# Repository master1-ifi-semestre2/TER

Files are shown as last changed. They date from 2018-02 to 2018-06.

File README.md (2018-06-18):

# Robot avec détection d’obstacles

Ce tutoriel vous guidera pas à pas dans la réalisation d'un robot explorateur détecteur d'obstacles.
Nous allons en réalité utiliser deux robots : 1 robot principal et 1 robot secondaire qui aura pour objectif de suivre le robot leader.

### Composants et outils
##### Robot de tête
Pour pouvoir construire le leader, vous aurez besoin de :
- 1 Arduino UNO (ou un autre type de microcontrôleur)
- 1 Shield Motor (Adafruit ou un autre type)
- 2 Moteurs avec roues adaptées aux moteurs
- 1 roue pivot
- 6 ultrasonic sensor HC-RC04
- 1 module emetteur sans fils 433Mhz (pour la communication radio fréquence)
- 1 boîtier pour 5 piles AA (de 1,2 V)
- des cables jumper
- 1 mini breadboard
- 1 chassis

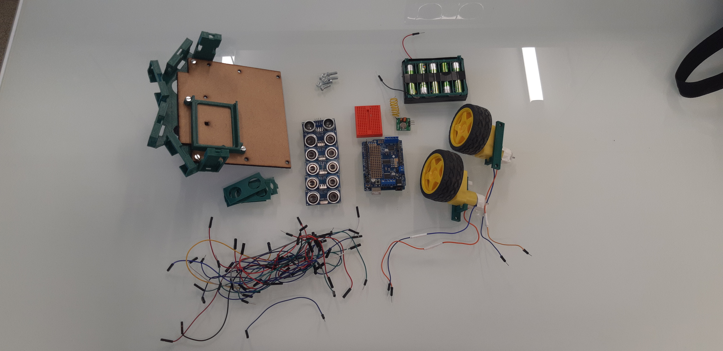
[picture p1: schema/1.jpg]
Les differents composant


##### Robot de queue
Pour construire le robot follower, vous aurez besoin de:
- 1 Arduino UNO
- 1 Shield Motor
- 2 Moteurs & leurs roues
- 1 roue libre
- 1 détecteurs de distance (ultrasonic sensor HC-RC04)
- 1 module récepteur sans fils 433Mhz (pour la communication radio fréquence)
- 1 boîtier pour 5 piles AA (de 1,2 V)
- des cables jumper
- 1 mini breadboard
- 1 chassi

#### Outils
- Une découpeuse Laser (utilisé pour faire le chassis des deux robots)
- Une imprimante 3D (utilisé pour imprimer certain accessoirs comme le pare-choc et le boîtier à piles...).
- Un éventuel kit de soudure si vos fils en ont besoin.

## Assembler le robot
Après vous être procuré tout ce materiel, commencez par retourner le chassis, puis fixez les moteurs.
<p align="center">
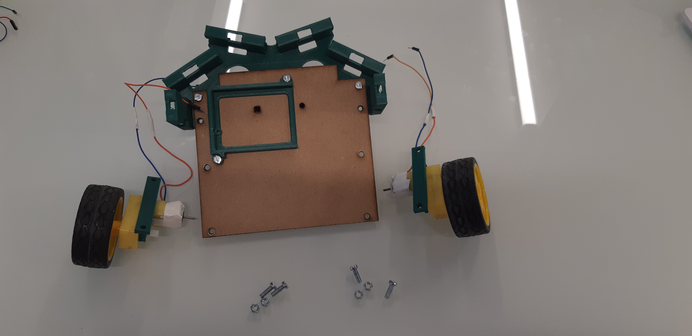
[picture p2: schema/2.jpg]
Chassi avec les Moteurs

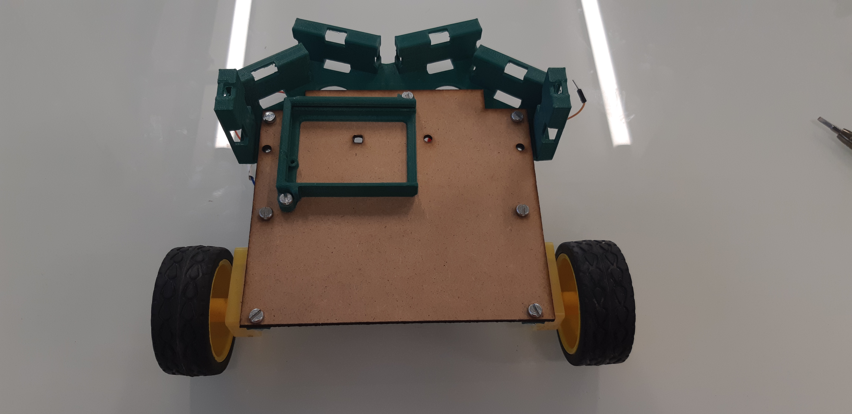
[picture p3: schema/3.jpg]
Moteurs monté

</p>

Montez ensuite le nez, puis les capteurs à ultrason. Nous conseillons de renverser un des capteurs centraux (pins vers le haut et pins vers le bas)afin d'éviter les interférence entre eux.

<p align="center">
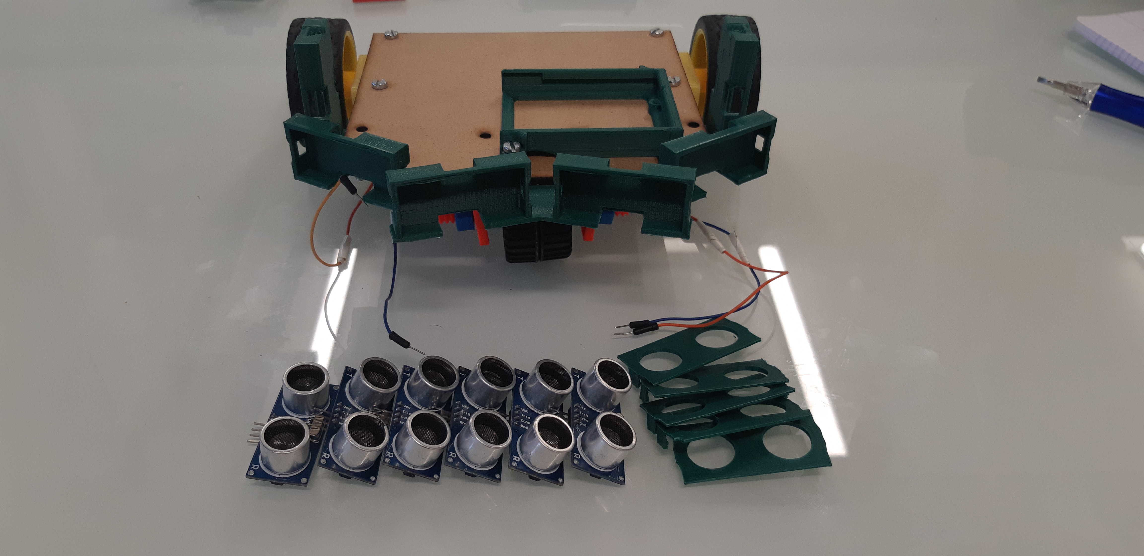
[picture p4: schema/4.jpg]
Ultrasonic Sensor avec Chassi

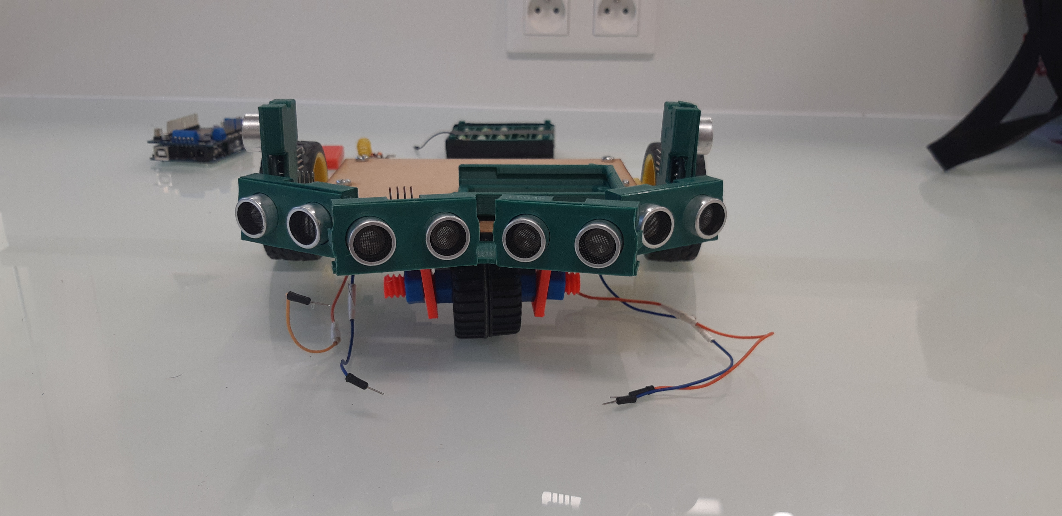
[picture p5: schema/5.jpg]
Sensor montés

</p>

Placez l'Arduino et la breadboard à l'emplacement désigné par l'image ci-dessous. Attention à ne pas oublier de relier Shield Motor avec l'Arduino, pour cela placez les connecteurs du Shield Motor sur ceux de l'Arduino.

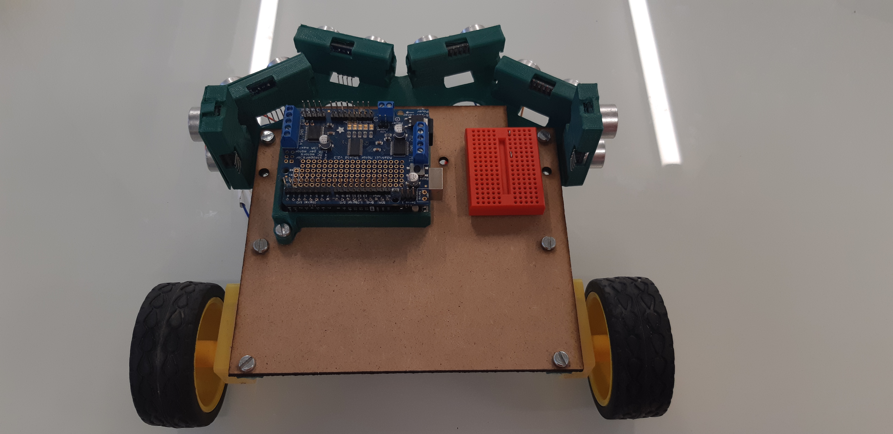
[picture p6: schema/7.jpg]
Arduino sur chassis Arduino sur chassi


## Les branchements

Attaquons nous aux branchements.
Commencez par relier les câbles des moteurs aux connecteurs du Shield Motor comme le montre l'image ci-dessous. Dans notre exemple nous avons utilisé les port M2 du Shield Motor pour la roued droite et M4 pour la roue gauche. Vous pouvez utiliser les numéros que vous voulez, cependant il faudra les modifier dans le code. Si les roues tournent à l'envers, pas de panique, il suffit juste d'inverser les câbles. Branchez ensuite les six capteurs toujours en suivant l'image en dessous, les GND (ground) entre GND, les VCC (5v) entre VCC, etc...

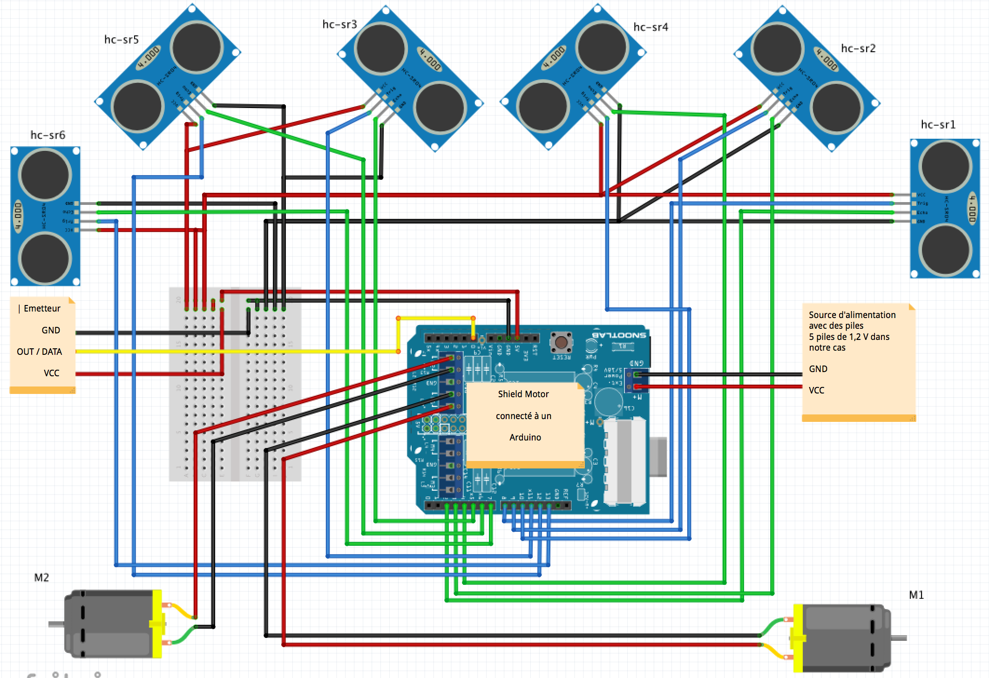
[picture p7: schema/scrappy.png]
Circuit du robot principal Circuit montage du Robot Leader

<p align="center">
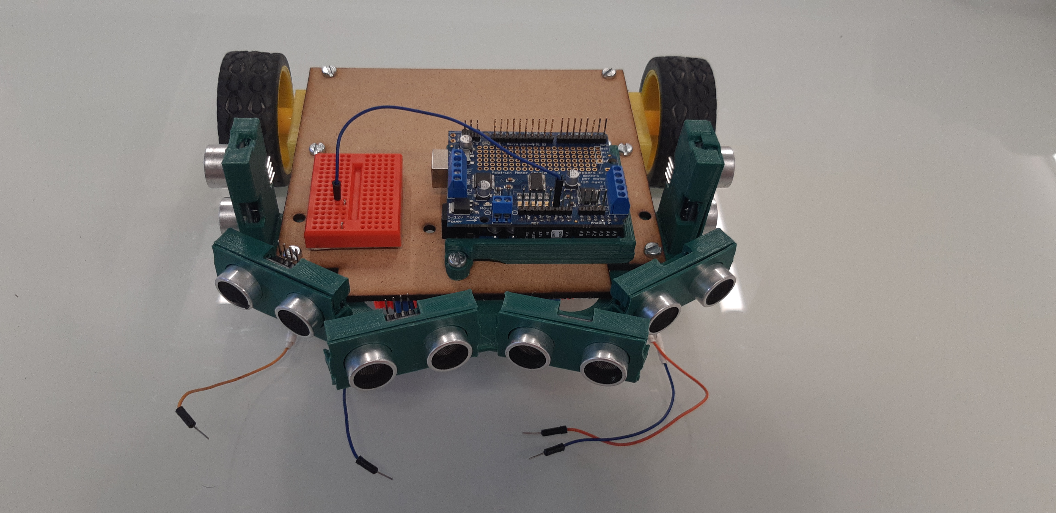
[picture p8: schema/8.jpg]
branchement 1

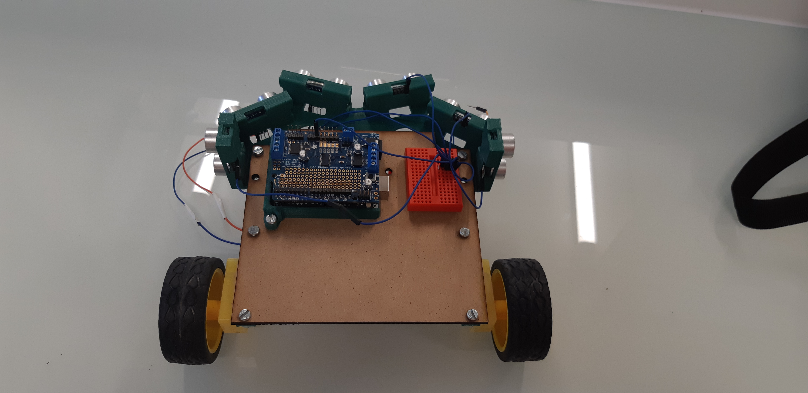
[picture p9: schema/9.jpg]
branchement 2

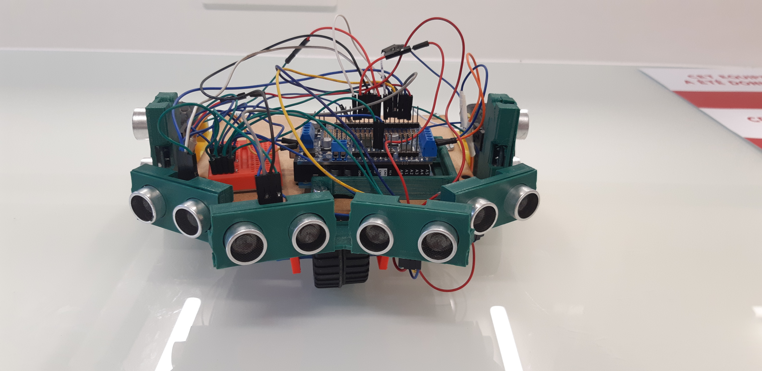
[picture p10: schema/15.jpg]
branchement 3


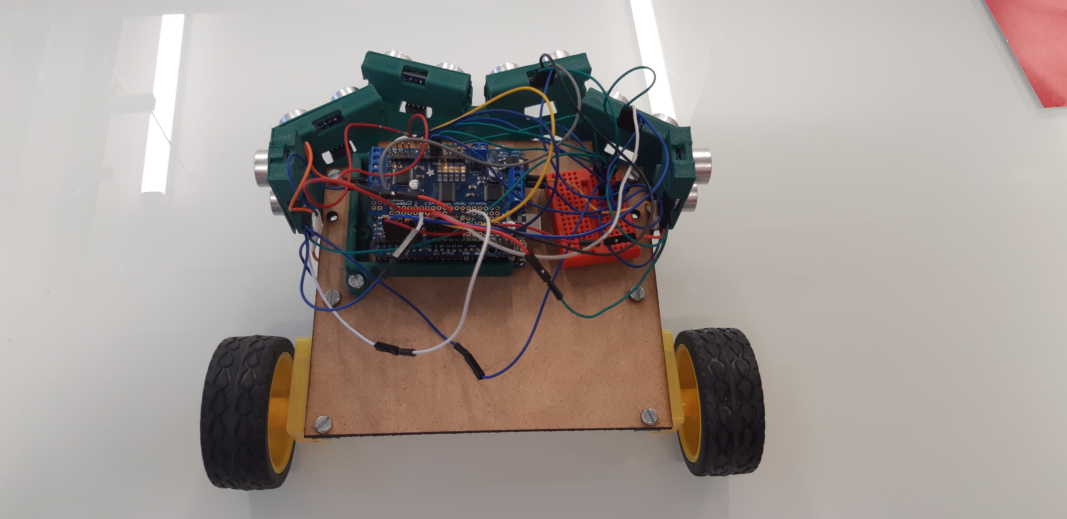
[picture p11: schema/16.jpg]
branchement 4

</p>

L'image qui suit montre l'Emetteur Radio Frequency 433Mhz. Son pin DATA est branché sur le pin A0 (ou pin 14) de l'Arduino (Arduino + Shield Motor).

<p align="center">
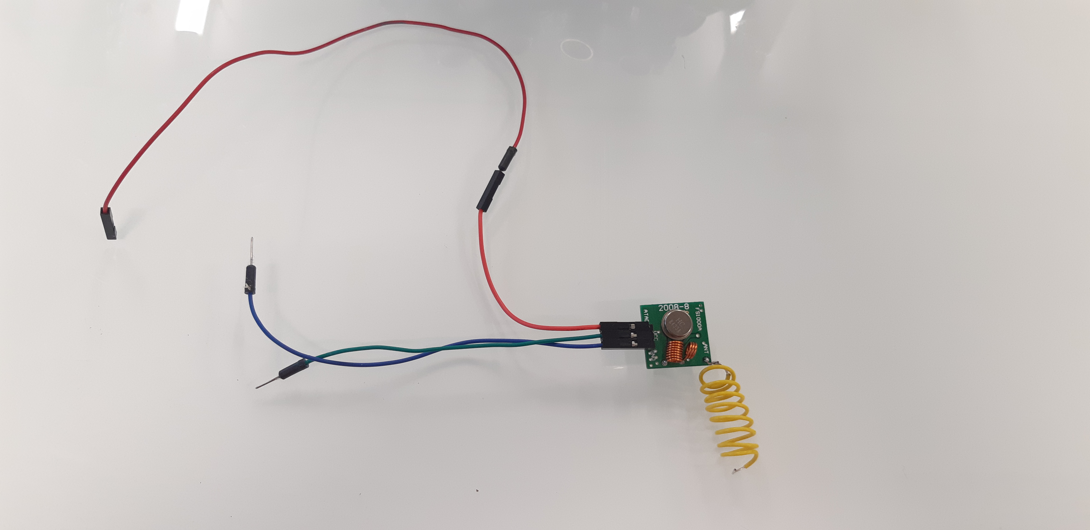
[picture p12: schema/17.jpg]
Emetteur RF 433Mhz

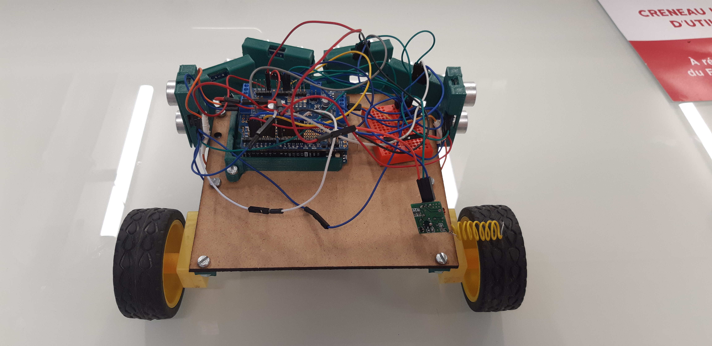
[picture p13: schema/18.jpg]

</p>

## L'alimentation
Pour alimenter le robot plusieurs solutions sont possibles : le port USB, une prise secteur (avec le bon chargeur), ou 5 piles AA.
Si vous optez pour une alimention via secteur ou USB vous devrez les connecter à l'Arduino.

Si vous optez pour une alimentation avec les piles alors le branchement se fait sur le Shield Motor (on peut aussi le relier à l'Arduino) comme on peut le voir sur l'image du circuit (les branchements) ci-dessus.
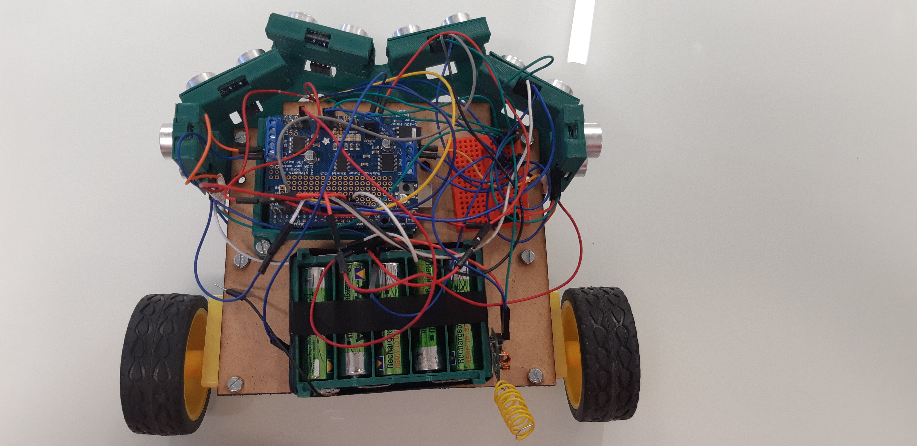
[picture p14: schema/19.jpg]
Robot avec Boîte à piles


## Installer le programme
Téléchargez et installez l'IDE Arduino, qui vous permettra de programmer les instructions avant de les envoyer sur la plaque. Il est disponible gratuitement [ici](https://www.arduino.cc/en/Main/Software).

## Programmer le robot
Pour programmer le robot il suffit de récuperer le code et de le téléverser depuis votre ordinateur vers l'Arduino utilisée.

## Utilisation de la découpe Laser
Idéal pour pour découper le chassis
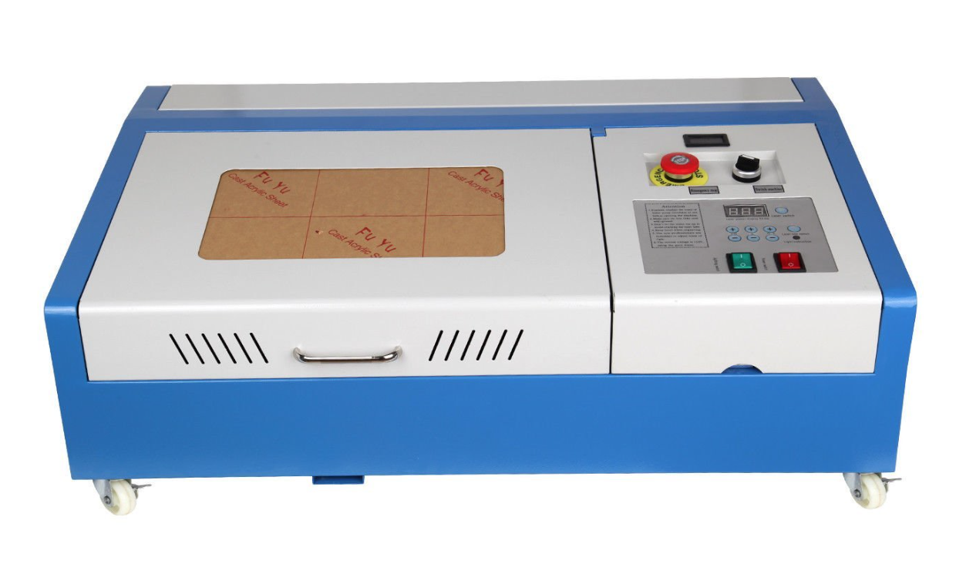
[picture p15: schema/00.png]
Découpe Laser


## Utilisation de l'imprimante 3D
Vous trouverez tous les plans gcode dans ce [dossier](https://github.com/master1-ifi-semestre2/TER/tree/master/plansIMPRESSIONS)

[Cliquez ici pour avoir les plans des elements a imprimer](https://github.com/master1-ifi-semestre2/TER/tree/master/plans3D)

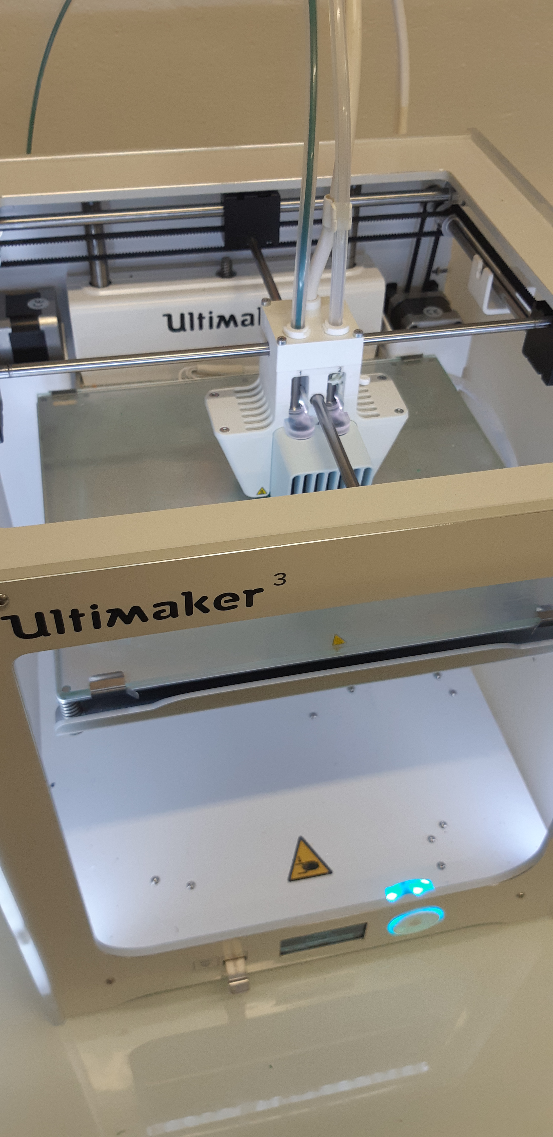
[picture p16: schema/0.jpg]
Ultimaker 3


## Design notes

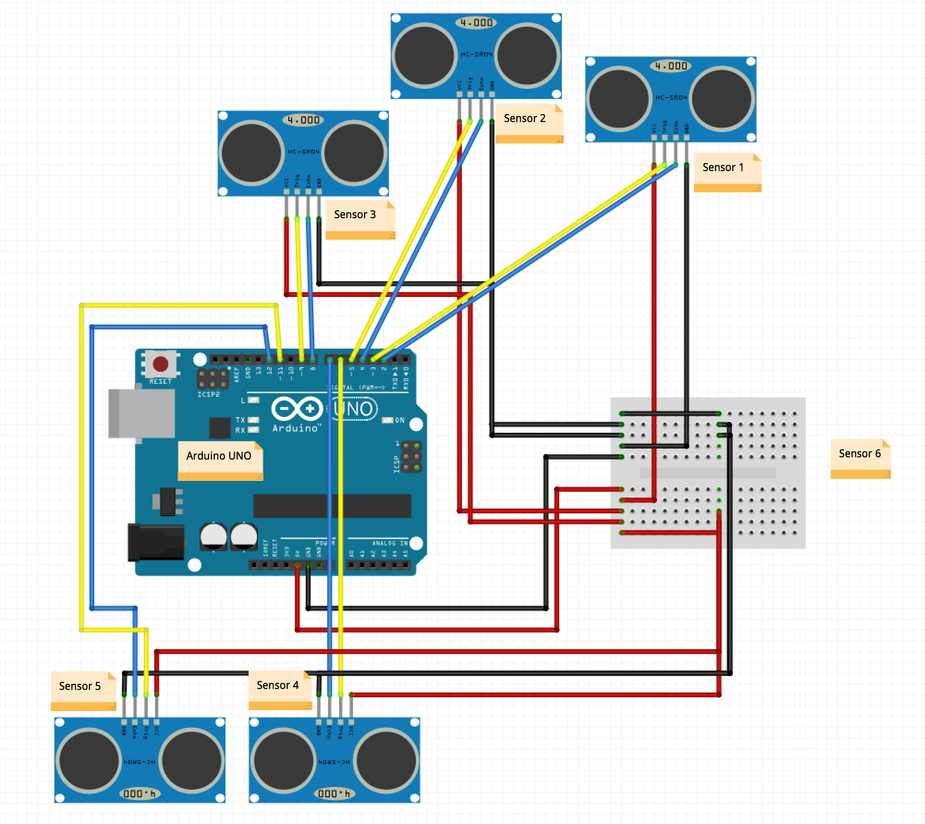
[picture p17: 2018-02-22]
sketch_avec_5_sensors.png

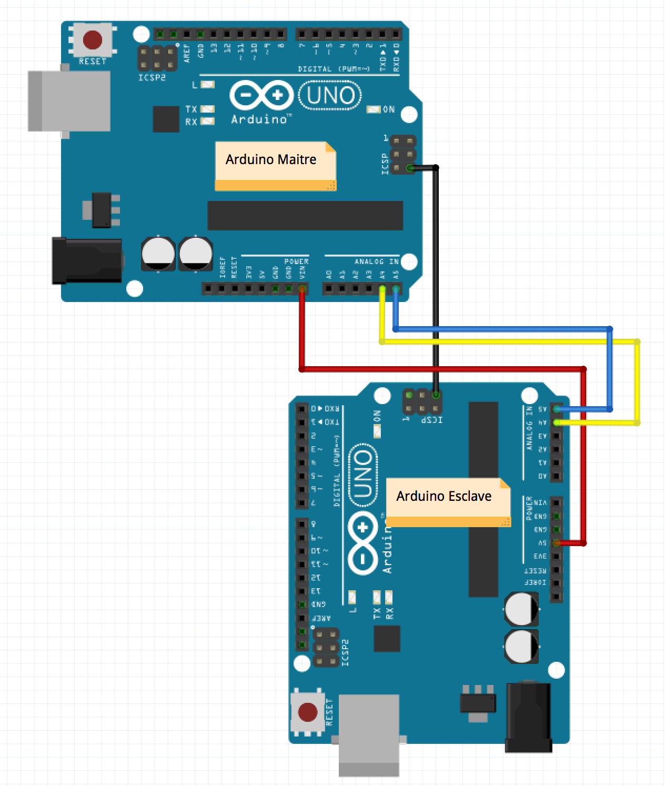
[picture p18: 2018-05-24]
schema/maitre_esclave.png

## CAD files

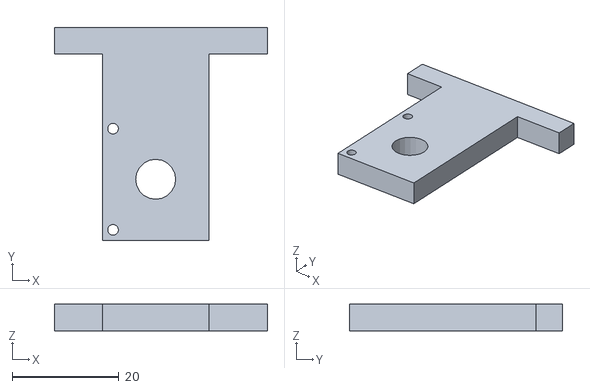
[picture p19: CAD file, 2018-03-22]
Copy of SENSOR TER PAR VUE.stl
40.0 x 40.0 x 5.00

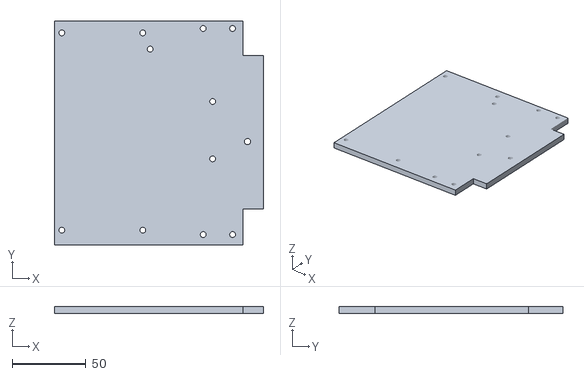
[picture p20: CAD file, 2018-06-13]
plans3D/chassis/chassisFinal.stl
142.0 x 152.0 x 5.00

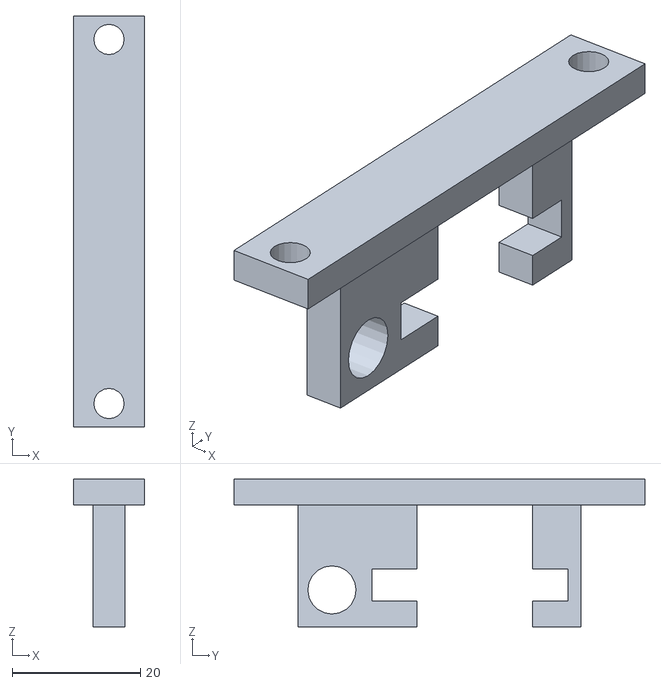
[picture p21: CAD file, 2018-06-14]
plans3D/moteur/support_moteur_v4.stl
11.0 x 64.0 x 23.0

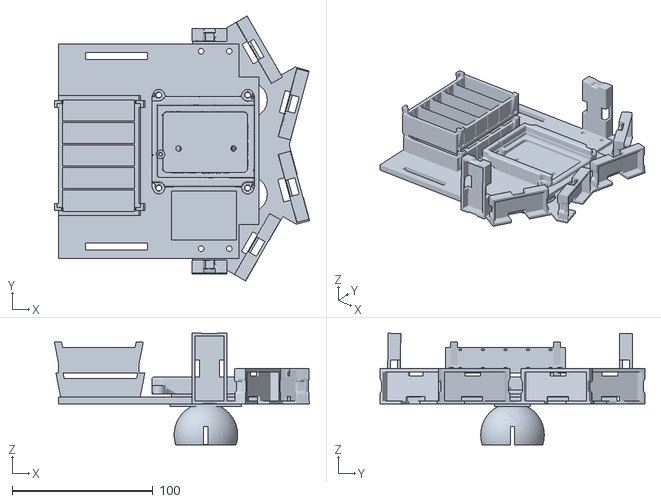
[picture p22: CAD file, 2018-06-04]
plans3D/plan_general.stl
181.1 x 188.0 x 79.1

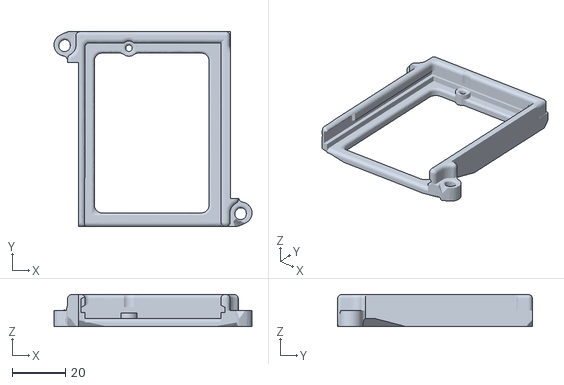
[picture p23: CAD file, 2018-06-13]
plans3D/support arduino/support_arduino_v2.stl
74.2 x 73.0 x 12.0

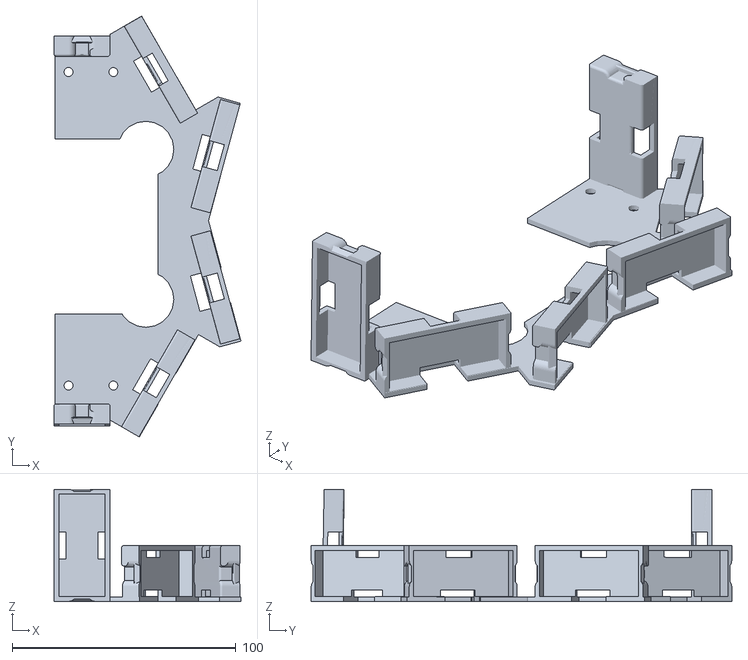
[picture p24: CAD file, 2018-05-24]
plans3D/yeux/yeux_v6.stl
83.5 x 188.0 x 50.1

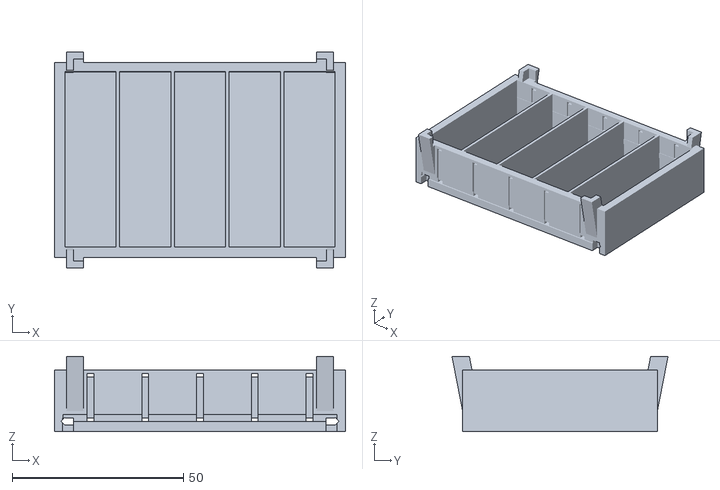
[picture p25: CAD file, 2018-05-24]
plans3D/5BatteryPack3-ard2.stl
85.0 x 63.1 x 22.0

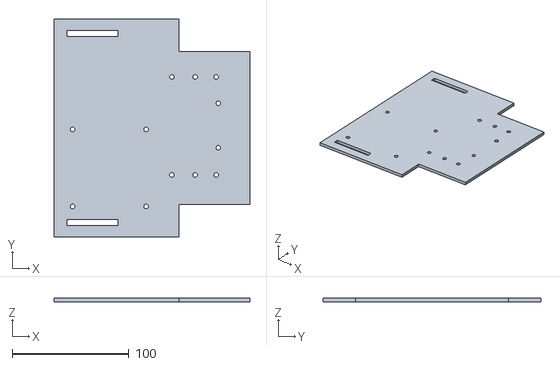
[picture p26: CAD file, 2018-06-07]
plans3D/chassis/chassis_nezExstant.stl
168.0 x 187.0 x 3.00

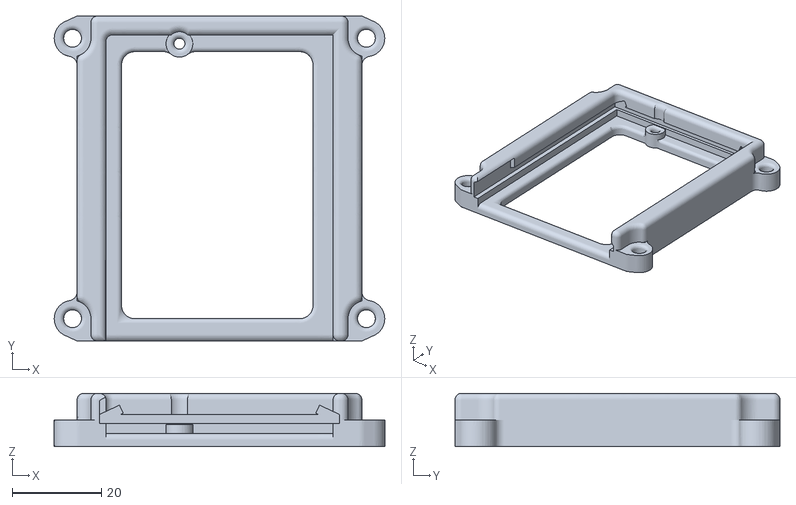
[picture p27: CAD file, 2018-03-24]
plans3D/support arduino/Arduino_mount1.stl
74.2 x 73.0 x 12.0

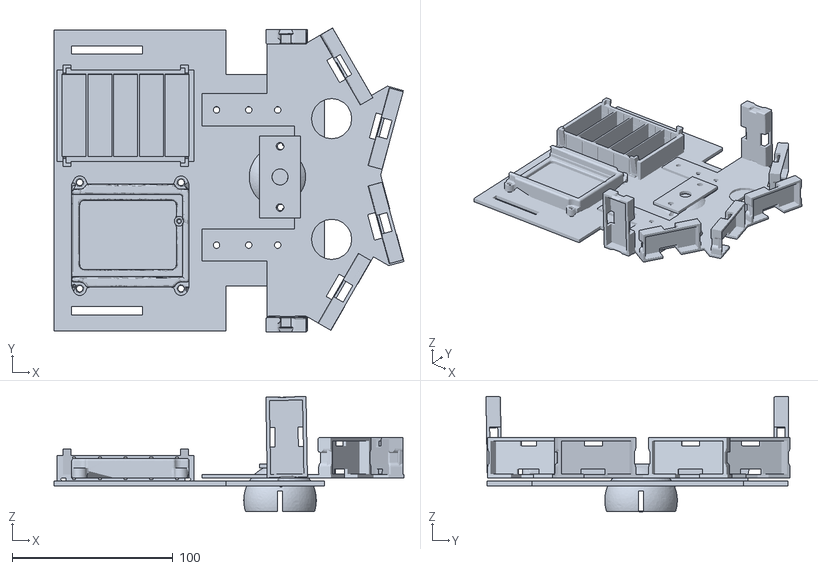
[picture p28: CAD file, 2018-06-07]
plans3D/chassis/planVersiongrande.stl
217.5 x 189.0 x 71.6

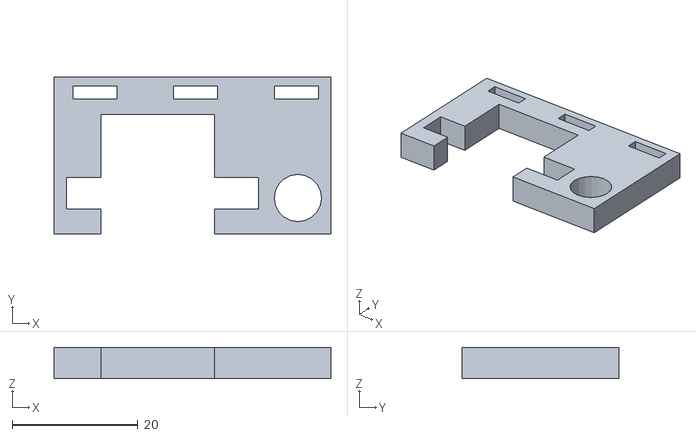
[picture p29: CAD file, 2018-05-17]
plans3D/moteur/MOTOR.stl
44.0 x 25.0 x 5.00

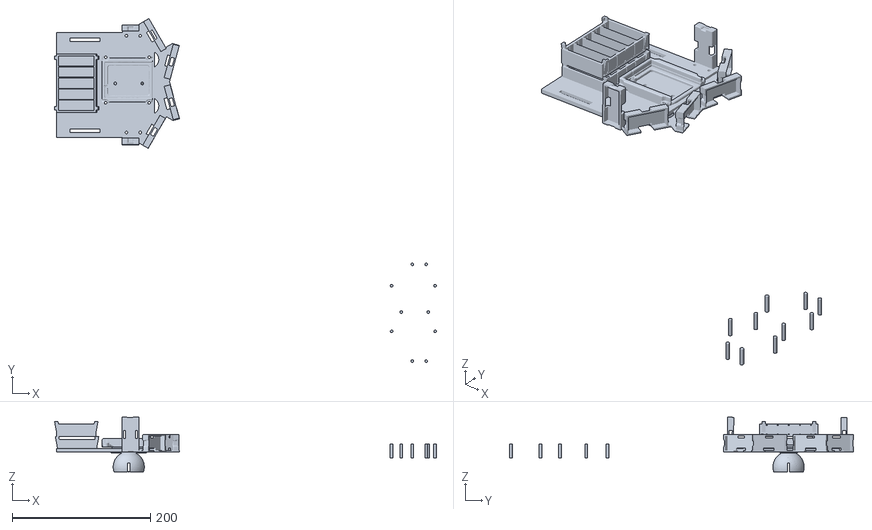
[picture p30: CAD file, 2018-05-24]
plans3D/scrappy.stl
553.1 x 498.0 x 79.1

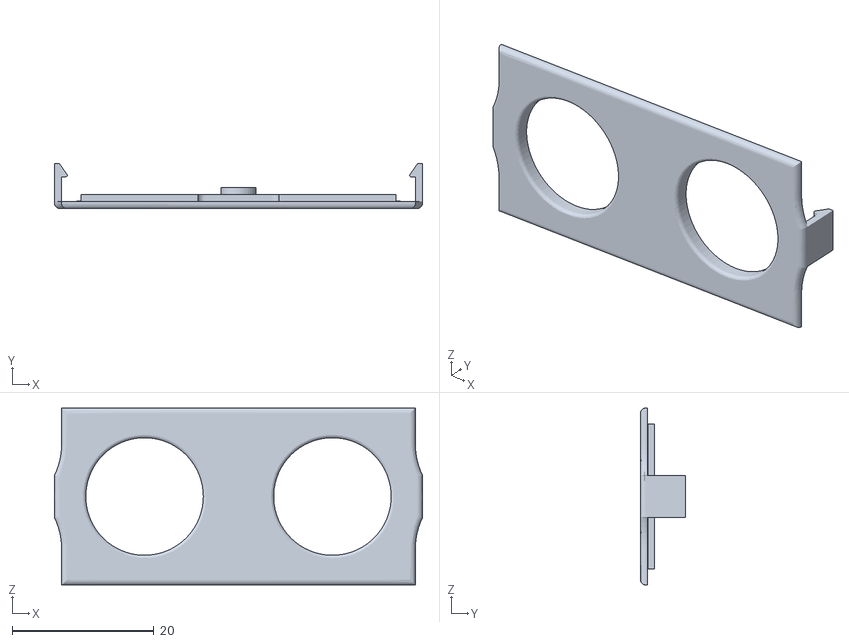
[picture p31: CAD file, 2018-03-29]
plans3D/HC_SR04_topCase_FINAL.stl
52.0 x 6.40 x 25.0

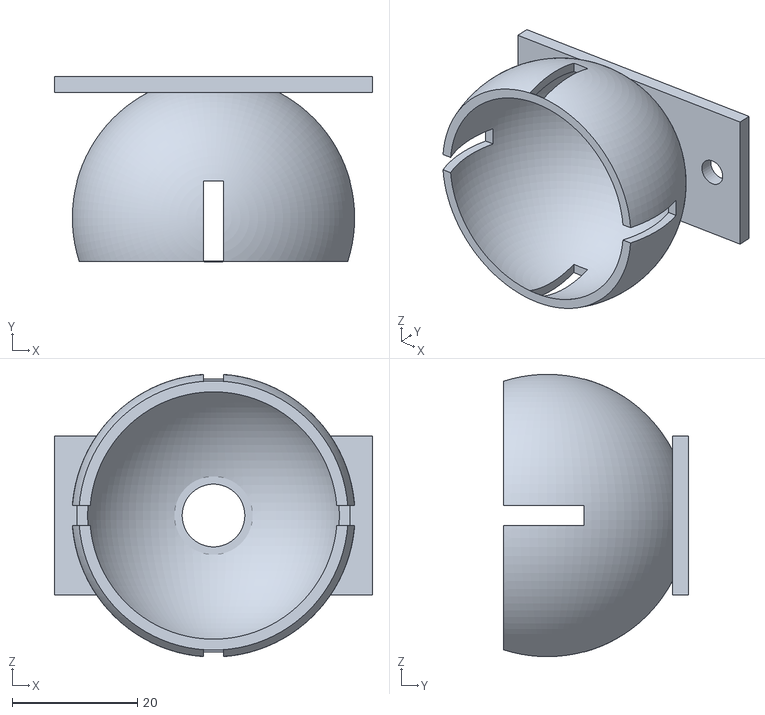
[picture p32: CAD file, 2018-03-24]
plans3D/pingpongwheel4.stl
50.8 x 29.6 x 45.1

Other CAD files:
plans3D/chassis/chassis_v2.stl
plans3D/chassis/Support.stl
plans3D/yeux/yeux_3.1.stl
plans3D/yeux/yeux_3.0.stl
plans3D/chassis/chassis_v1.stl
plans3D/moteur/support_moteur_v2.stl
plans3D/yeux/yeux_1.0.stl
plans3D/yeux/yeux_2.0.stl
plans3D/yeux/yeux_v3.2.stl
plans3D/yeux/yeux_v3.3.stl
plans3D/yeux/yeux_v4.0.stl
plans3D/yeux/yeux_v5.0.stl
plans3D/yeux/yeux_v5.1.stl

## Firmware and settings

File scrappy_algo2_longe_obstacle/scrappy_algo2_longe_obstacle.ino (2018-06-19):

/****************************************************************************
   Sonar Robot

   Authors:  
      - BENSOUSSAN Chloé
      - BOUKOU Grâce
      - GRÉAU Alexandre      
      - WILHELM Andreina
          
   Permissions: MIT licence
      
*****************************************************************************/

#include <Adafruit_MotorShield.h>

#define FORWARD_ 0
#define BACKWARD_ 2
#define LEFT_ -1
#define RIGHT_ 1


/* Ultrasonic sensors */      
const uint8_t echoPin_RIGHT = 2;  // echo signal (receives)
const uint8_t echoPin_right = 3;
const uint8_t echoPin_front_right = 4;
const uint8_t echoPin_front_left = 5; 
const uint8_t echoPin_left = 6;
const uint8_t echoPin_LEFT = 7; 

const uint8_t trigPin_RIGHT = 8;  // trigger signal (sends)
const uint8_t trigPin_right = 9;
const uint8_t trigPin_front_right = 10;
const uint8_t trigPin_front_left = 11; 
const uint8_t trigPin_left = 12;
const uint8_t trigPin_LEFT = 13;


/* Measurements */
const float safetyDistance = 30; // according with the speed. Expressed in cm
const float robotWidth = 20; // expressed in cm
const float marge = safetyDistance / 3; // margin of movement. It should move between the marging and the safetyDistance


/* LEDs
 * long side : pin
 * short side : ground
 * resistor : 100 Ohm
 */
const uint8_t ledPin_left = 15;
const uint8_t ledPin_back = 16;
const uint8_t ledPin_right = 17;


/*
 * Determines where to move
 */
int objectDetected = 0; // the side where the object is detected
boolean searchingObject = false;
int tick = 0;
int randomDir = FORWARD_;
boolean stop_ = false;


/* Movement */
const int motorSpeed = 200; // from 0 (off) to 255 (max speed)

// Create the motor shield object with the default I2C address
Adafruit_MotorShield AFMS = Adafruit_MotorShield();
// Or, create it with a different I2C address (say for stacking)
// Adafruit_MotorShield AFMS = Adafruit_MotorShield(0x61); 

// Motor 4 -> left / Motor 2 -> right
Adafruit_DCMotor *motorLeft = AFMS.getMotor(4);
Adafruit_DCMotor *motorRight = AFMS.getMotor(2);


/*
 * Motors setup and movement
 */ 
void setupMotors() {
  // Left wheel
  motorLeft->setSpeed(motorSpeed);
  motorLeft->run(FORWARD);
  motorLeft->run(RELEASE);
  
  // Right wheel
  motorRight->setSpeed(motorSpeed);
  motorRight->run(FORWARD);
  motorRight->run(RELEASE);
}

void moveForward() {
  motorRight->run(FORWARD);
  motorLeft->run(FORWARD);
}

void moveBackward() {
  motorRight->run(BACKWARD);
  motorLeft->run(BACKWARD);

  // turn on back led
  // turnOnLed(ledPin_back);
}

void moveLeft() {
  motorLeft->run(RELEASE);
  motorRight->run(FORWARD);

  // turn on left led
  // turnOnLed(ledPin_left);
}

void moveRight() {
  motorLeft->run(FORWARD);
  motorRight->run(RELEASE);

  // turn on right led
  // turnOnLed(ledPin_right);
}

void dontMove() {
  motorLeft->run(RELEASE);
  motorRight->run(RELEASE);
}



/*
 * LEDs setup
 */ 
void setupLeds() {
  pinMode(ledPin_left, OUTPUT);
  pinMode(ledPin_back, OUTPUT);
  pinMode(ledPin_right, OUTPUT);  
}

void turnOffAllLeds() { 
  digitalWrite(ledPin_left, LOW);
  digitalWrite(ledPin_back, LOW);
  digitalWrite(ledPin_right, LOW);
  delay(100);
}

void turnOnLed(uint8_t ledPin) {
  digitalWrite(ledPin, HIGH);  
}



/*
 * Calculates the distance with the information obtained from the sensors  
 */
float calculDistance(uint8_t trigPin, uint8_t echoPin){
  uint32_t duration; // duration of the round trip
  float cm;  // distance of the obstacle

  // The sensor is triggered by a HIGH pulse of 10 or more microseconds.
  // Give a short LOW pulse beforehand to ensure a clean HIGH pulse:
  pinMode(trigPin, OUTPUT);
  digitalWrite(trigPin, LOW);
  delayMicroseconds(3);

  // Start trigger signal

  digitalWrite(trigPin, HIGH);
  delayMicroseconds(10);
  digitalWrite(trigPin, LOW);
 
  // Read the signal from the sensor: a HIGH pulse whose
  // duration is the time (in microseconds) from the sending
  // of the ping to the reception of its echo off of an object.

  pinMode(echoPin, INPUT);
  duration = pulseIn(echoPin, HIGH);
 
  // convert the time into a distance
  cm = (float)((duration<<4)+duration)/1000.0; // cm = 17 * duration/1000
  return cm;
}


void initValue() {
  objectDetected = 0;
  searchingObject = false;
  tick = 0;
}

/*
 * Determines where to move
 */
int explore(float cm_LEFT, float cm_left, float cm_front_left, float cm_front_right, float cm_right, float cm_RIGHT) {  
  
  /* Print distance of each sensor - for debugging
  Serial.print("object detected (-1 == left) ");
  Serial.println(objectDetected);
  Serial.print(cm_LEFT);
  Serial.print(" - ");
  Serial.print(cm_left);
  Serial.print(" - ");
  Serial.print(cm_front_left);
  Serial.print(" - ");
  Serial.print(cm_front_right);
  Serial.print(" - ");
  Serial.print(cm_right);
  Serial.print(" - ");
  Serial.println(cm_RIGHT);
  */
   
 if (tick > 203) {
  initValue();
  stop_ = false;
 }
 else if (tick == 200) {
      randomDir = -objectDetected;
      stop_ = true;
      return randomDir;
  }
  
 if (searchingObject && objectDetected == LEFT_){
    // Turn until robot is parallel to the object
    if (cm_LEFT < safetyDistance ||  cm_left < safetyDistance){
         searchingObject = false;
    }
    else {
        // Serial.println(" Tourne à droite pour retrouver l'object ");
         return RIGHT_;
    }
 }
 else if (searchingObject && objectDetected == RIGHT_){
    // Turn until robot is parallel to the object
    if (cm_RIGHT < safetyDistance ||  cm_right < safetyDistance){
         searchingObject = false;
    }
    else {
        // Serial.println(" Tourne à gauche pour retrouver l'object ");
         return LEFT_;
    }
 }

 if (objectDetected == LEFT_) {
      // If there is already an object detected
      if(cm_LEFT > safetyDistance && cm_left > safetyDistance) {
        // If there is an object detected on the left and he has passed it, then he has to turn left
        return LEFT_;
      } 
      if (cm_LEFT < safetyDistance - marge ||  cm_left < safetyDistance - marge || cm_front_right < safetyDistance || cm_front_left < safetyDistance){
        return RIGHT_;
      } 
    return FORWARD_; 
  } 
  else if (objectDetected == RIGHT_) {
      // If there is already an object detected
      if(cm_RIGHT > safetyDistance && cm_right > safetyDistance) {
        // If there is an object detected on the left and he has passed it, then he has to turn right
        return RIGHT_;
      } 
      if (cm_RIGHT < safetyDistance - marge ||  cm_right < safetyDistance - marge || cm_front_right < safetyDistance || cm_front_left < safetyDistance){
          return LEFT_;
      } 
    return FORWARD_; 
  }
  else {
    // There's no object detected
    if (tick < 4) {
      return randomDir; 
    }
    
    if(cm_LEFT < safetyDistance || cm_left < safetyDistance) {
        // Object detected on the left side
         objectDetected = LEFT_;
     }
     else if(cm_RIGHT < safetyDistance || cm_right < safetyDistance) {
        // Object detected on the right side
         objectDetected = RIGHT_;
     }
     else if(cm_front_left < safetyDistance && cm_front_right < safetyDistance) {
        // Object detected in front of him
        
        if(cm_LEFT < safetyDistance || cm_left < safetyDistance) {
            // There is an object on the left side 
            objectDetected = LEFT_;
            return RIGHT_;
        }
        else if(cm_RIGHT < safetyDistance || cm_right < safetyDistance) {
            // There is an object on the right side
            objectDetected = RIGHT_;
            return LEFT_;
        }
        else {
            // Compare both sides
            if  (cm_right > cm_left) {
                objectDetected = LEFT_;
                searchingObject = true;
                return RIGHT_;
            }
            else {
              //Serial.println(" - RIGHT");
              objectDetected = RIGHT_;
              searchingObject = true;
              return LEFT_;
            }  
        }       
     }
     return FORWARD_; 
  }
} 



/*
 * Moves the wheels
 */
void navigate(){
  int resultatExplore;
  
  float cm_front_left;  // distance of the obstacle
  float cm_front_right;
  float cm_left;
  float cm_LEFT;
  float cm_right;
  float cm_RIGHT;

  
  noInterrupts();
  cm_front_left = calculDistance(trigPin_front_left, echoPin_front_left);
  cm_front_right = calculDistance(trigPin_front_right, echoPin_front_right);
  cm_left = calculDistance(trigPin_left, echoPin_left);
  cm_LEFT = calculDistance(trigPin_LEFT, echoPin_LEFT);
  cm_right = calculDistance(trigPin_right, echoPin_right);
  cm_RIGHT = calculDistance(trigPin_RIGHT, echoPin_RIGHT);

  resultatExplore = explore(cm_LEFT, cm_left, cm_front_left, cm_front_right, cm_right, cm_RIGHT);
  interrupts();

  tick++;

  if (stop_){
    dontMove();
    return;
  }
  
  // turn off leds
  // turnOffAllLeds();
  
  motorRight->run(RELEASE);
  motorLeft->run(RELEASE);

  switch(resultatExplore) {
    // move forward  
    case FORWARD_:  
      //Serial.print("avant  ");
      moveForward();
      break;

    // move backward
    case BACKWARD_:
      //Serial.print("arriere  ");
      moveBackward();
      break;

    // move left
    case LEFT_: 
      //Serial.print("gauche  ");
      moveLeft();
      break;

    // move right
    case RIGHT_:
      //Serial.print("droite  ");
      moveRight();
      break;
  }
}


/*
 * Initial setup
 */
void setup() {
  // initialize serial communication:
  Serial.begin(9600);
  AFMS.begin();  // create with the default frequency 1.6KHz
  
  setupMotors();
  //setupLeds();
}


/*
 * It's the function that will be called at each tick time
 */
void loop()
{
  navigate();
}

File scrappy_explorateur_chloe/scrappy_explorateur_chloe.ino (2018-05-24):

/****************************************************************************
   Sonar Robot

   Authors:  
      - BENSOUSSAN Chloé
      - BOUKOU Grâce
      - GRÉAU Alexandre      
      - WILHELM Andreina
          
   Permissions: MIT licence
      
*****************************************************************************/

#include <Wire.h>
#include <Adafruit_MotorShield.h>
#include <Adafruit_PWMServoDriver.h>
#include <TimerOne.h>
#include <VirtualWire.h>

#define FORWARD_ 0
#define BACKWARD_ 2
#define LEFT_ -1
#define RIGHT_ 1


/* Ultrasonic sensors */
const uint8_t trigPin_LEFT = 10;
const uint8_t echoPin_LEFT = 11;

const uint8_t trigPin_left = 5;
const uint8_t echoPin_left = 4;

const uint8_t trigPin_front_left = 2; // trigger signal (sends)
const uint8_t echoPin_front_left = 3; // echo signal (receives)

const uint8_t trigPin_front_right = 12;
const uint8_t echoPin_front_right = 13;

const uint8_t trigPin_right = 7;
const uint8_t echoPin_right = 6;

const uint8_t trigPin_RIGHT = 8;
const uint8_t echoPin_RIGHT = 9;


/* Communication */
const int transmit_pin = 17;    
const uint8_t myId = 0; // boss

typedef struct {
  int id;
  int value;
} Message;

Message msg;


/* Measurements */
const float safetyDistance = 27; // according with the speed, expressed in cm
const float robotWidth = 20; // and the height is 12 cm


/* LEDs
 * long side : pin
 * short side : ground
 * resistor : 100 Ohm
 */
const uint8_t ledPin_left = 14;
const uint8_t ledPin_back = 15;
const uint8_t ledPin_right = 16;


/* Movement */
volatile int currentState = FORWARD_; // initial state = forward
const int motorSpeed = 110;

/*
 * Determines where to move
 */
int objectDetected = 0; // 0 false, !0 true
boolean searchingObject = false;
int tick = 0;
int randomDir = FORWARD_;

// Create the motor shield object with the default I2C address
Adafruit_MotorShield AFMS = Adafruit_MotorShield();
// Or, create it with a different I2C address (say for stacking)
// Adafruit_MotorShield AFMS = Adafruit_MotorShield(0x61); 

// Motor 1 -> right Motor 2 -> left
Adafruit_DCMotor *motorRight = AFMS.getMotor(1);
Adafruit_DCMotor *motorLeft = AFMS.getMotor(2);


void initValue(){
  currentState = FORWARD_;
  objectDetected = 0;
  searchingObject = false;
  tick = 0;
}

/*
 * Calculates the distance with the information obtained from the sensors  
 */
float calculDistance(uint8_t trigPin,uint8_t echoPin){
  uint32_t duration; // duration of the round trip
  float cm;  // distance of the obstacle

  // The sensor is triggered by a HIGH pulse of 10 or more microseconds.
  // Give a short LOW pulse beforehand to ensure a clean HIGH pulse:
  pinMode(trigPin, OUTPUT);
  digitalWrite(trigPin, LOW);
  delayMicroseconds(3);

  // Start trigger signal

  digitalWrite(trigPin, HIGH);
  delayMicroseconds(10);
  digitalWrite(trigPin, LOW);
 
  // Read the signal from the sensor: a HIGH pulse whose
  // duration is the time (in microseconds) from the sending
  // of the ping to the reception of its echo off of an object.

  pinMode(echoPin, INPUT);
  duration = pulseIn(echoPin, HIGH);
 
  // convert the time into a distance
  cm = (float)((duration<<4)+duration)/1000.0; // cm = 17 * duration/1000
  return cm;
}

int explore(float cm_LEFT, float cm_left, float cm_front_left, float cm_front_right, float cm_right, float cm_RIGHT) {  
  Serial.print(cm_LEFT);
  Serial.print(" - ");
  Serial.print(cm_left);
  Serial.print(" - ");
  //Serial.print(cm_front_left);
  Serial.print(" - ");
  //Serial.print(cm_front_right);
  Serial.print(" - ");
  Serial.print(cm_right);
  Serial.print(" - ");
   Serial.println(cm_RIGHT);
   
  if (tick < 3){
    return randomDir; 
  }

  if (tick > 200){
      Serial.println("random");
      randomDir = objectDetected;
      initValue();
      return -randomDir;
  }
  
 if (searchingObject == true && objectDetected == LEFT_){
    /* Tourner jusqu'à être parallèle à l'objet */
    if (cm_LEFT < safetyDistance ||  cm_left < safetyDistance){
         searchingObject = false;
    }
    else {
        // Serial.println(" Tourne à droite pour retrouver l'object ");
         return RIGHT_;
    }
 }
 else if (searchingObject == true && objectDetected == RIGHT_){
    /* Tourner jusqu'à être parallèle à l'objet */
     if (cm_RIGHT < safetyDistance ||  cm_right < safetyDistance){
         searchingObject = false;
    }
    else {
        // Serial.println(" Tourne à gauche pour retrouver l'object ");
         return LEFT_;
    }
 }

 if (objectDetected == LEFT_) {
      // Si il a déjà détecté un objet
      if(cm_LEFT > safetyDistance && cm_left > safetyDistance) {
        /* Object detected in left side, and he has pass the object, then he has to turn in left */
        return LEFT_;
      } 
      if (cm_LEFT < safetyDistance - 10 ||  cm_left < safetyDistance - 10 || cm_front_right < safetyDistance || cm_front_left < safetyDistance){
        return RIGHT_;
      } 
    return FORWARD_; 
  } 
  else if (objectDetected == RIGHT_) {
      
      // Si il a déjà détecté un objet
      if(cm_RIGHT > safetyDistance && cm_right > safetyDistance) {
        /* Object detected in left side, and he has pass the object, then he has to turn in left */
        return RIGHT_;
      } 
      if (cm_RIGHT < safetyDistance - 10 ||  cm_right < safetyDistance - 10 || cm_front_right < safetyDistance || cm_front_left < safetyDistance){
          return LEFT_;
      } 
    return FORWARD_; 
  }
  else {
    /* Pas d'object détecté !!*/

    if(cm_LEFT < safetyDistance || cm_left < safetyDistance) {
        /* Detected an object in left side */
         objectDetected = LEFT_;
     }
     else if(cm_RIGHT < safetyDistance || cm_right < safetyDistance) {
        /* Detected an object in right side */
         objectDetected = RIGHT_;
     }
     else if(cm_front_left < safetyDistance || cm_front_right < safetyDistance) {
        /* He detects an object in front of him */
        
        if(cm_LEFT < safetyDistance || cm_left < safetyDistance) {
            /* There is an object on left side */
            objectDetected = LEFT_;
            return RIGHT_;
        }
        else if(cm_RIGHT < safetyDistance || cm_right < safetyDistance) {
            /* There is an object on right side */
            objectDetected = RIGHT_;
            return LEFT_;
        }

        else {
            /* Compare both side */
            if  (cm_right > cm_left){
                objectDetected = LEFT_;
                searchingObject = true;
                return RIGHT_;
            }
            else {
              //Serial.println(" - RIGHT");
              objectDetected = RIGHT_;
              searchingObject = true;
              return LEFT_;
            }  
        }       
     }
     return FORWARD_; 
  }
}
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

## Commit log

2018-02-22 Ajout du code source de l'année passée
2018-02-22 Ajout de l'image du circuit avec 5 sensors
    Télécharger Fritzing pour pouvoir modifier
    [sketch_ter.fzz]
2018-02-22 Suppression boucle avant/arrière TODO : temps de calcul trop lent
2018-03-01 ✓ Déplacement de Scrappy correct
2018-03-01 Ajout capteur devant pour les angles morts
2018-03-01 ✓ Correction de petites erreurs ✓ S'il a de la place pour touner, il tourne jusqu'a qu'il trouve de la place pour avancer (Ne tourne plus à droite et a gauche en continue -> il continue de tourner da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
2018-03-15 ✓ Ajout code pour la communication : Scrappy -> recepteur
2018-03-15 Petite modification de l'émetteur
2018-03-15 ✓ Envoie de valeur, tableau, struct
2018-03-15 Organisation des fichiers
2018-03-15 Transmettre les bonnes valeurs de la direction (en cours)
2018-03-15 ✓ Envoie de données (direction) ✗ Calculs distances fausses de temps en temps (tourne quand il ne faut pas)
2018-03-22 ✓ Communication parfaite unidirectionnelle dans la même salle
2018-03-22 ✗ Echec LED (a cause des fonctions d'envoi de messages)
2018-03-22 ✓Mise a jour de scrappy_émetteur
2018-03-22 ajouter led arriere et changement de transmitter en anglais
2018-03-24 plans 3D création
    Arduino
    Roue direction
    "pare choc" v1.0 & 2.0 : INCOMPLET
    capuchon clipsable parechoc
    [Arduino_mount1.stl, HC-SR04_top_case.stl, pingpongwheel4.stl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]
2018-03-26 new version nez
    [yeux_3.0.stl]
2018-03-27 fin yeux;trous boulons de 3mm
    [yeux_final.stl]
2018-03-29 ✓ LED arrière avec Résistor ✗ problème de reception de message (fonctionne que de temps en temps)
2018-03-29 petites modifications LED
2018-03-29 update yeux
    trous pour les fiches
    [yeux_3.1.stl, yeux_v3.2.stl, yeux_v3.3.stl]
2018-03-29 tout les LEDs marche
2018-03-29 top case final
    [HC-SR04_top_case.stl, HC_SR04_topCase_FINAL.stl]
2018-04-12 Safety distance à 10 cm et augmentation vitesse (l'algo marche bien avece 150° entre les deux capteurs devant avec une vitesse pas trop grande --> 255 NG)
2018-04-12 Mise à jour de transmitter car changement d'angle des capteurs gauche et droite
2018-04-12 yeux v4
    [yeux_v4.0.stl]
2018-04-20 Continue algo explorateur ✓ Début tourne un peu autour de l'objet
2018-04-20 ✓ Code plus clair !
2018-04-20 yeux version 6 capteurs
    [yeux_v5.0.stl]
2018-04-23 differente disposition pour nez
    capteurs lateraux couchés
    [yeux_v5.1.stl]
2018-05-17 correction de communication
2018-05-24 Démonstration pour les CM2
2018-05-24 yeux v6
    [yeux_v6.stl]
2018-05-24 Random dans scrappy_explorateur, fonctionne pas bien quand il longe le mur
2018-05-24 Plans chassis sans batteries
    [Support.stl, chassis_v1.stl]
2018-05-24 idee generale de scrappy et nouveau batterie pack
    [5BatteryPack3-ard2.stl, scrappy.stl]
2018-05-24 nouveau chassis
    support arduino rotated pour laisser place aux batteries
    [chassis_v2.stl]
2018-06-04 plan general ideal
    [plan_general.stl]
2018-06-04 PLan Bis de scrappy avec nez existant
    [chassis_nezExstant.stl]
2018-06-07 Chassis update
    [chassis_nezExstant.stl, planVersiongrande.stl]
2018-06-11 Mise à jour des pins et organisation des codes
2018-06-11 Modification motor
2018-06-12 petites corrections et suiveur
    [scrappy_algo1_evite_obstacle.ino, scrappy_algo2_longe_obstacle.ino, scrappy_junior_suiveur.ino]
2018-06-13 UPdate support arduino
    [Arduino_mount1.stl, support_arduino_v2.stl]
2018-06-13 chassis v2
    [Arduino_mount1.stl]
2018-06-13 Schema du circuit de Scrappy Junior :+1:
    [scrappy_junior.fzz]
2018-06-13 correction motors algo2
2018-06-13 Mise a jour du tuto 1
    [scrappy.fzz, scrappy_junior_arduino_shield_motor.fzz, scrappy_junior_shield_motor_motor.fzz]
2018-06-13 update plan support moteur
    [MOTOR.stl, support_moteur_v2.stl]
2018-06-13 Update support moteur
    [supportMoteurV3.stl]
2018-06-14 update support moteur v 4
    [support_moteur_v4.stl]
2018-06-14 ✓ Amélioration algo 2 (fonctionne bien mais faire attention à l'angle de détection de l'obstacle au début)
2018-06-14 chagement librarie pour la comunnication
2018-06-17 PLans impressions
    [chassisFinal.stl]
2018-06-18 ✓ Ajout rapport final !!
2018-06-18 librarie de communication change et communication fait
2018-06-19 petites corrections et elimination de communication deuxieme algo
    [scrappy_algo1_evite_obstacle.ino, scrappy_algo2_longe_obstacle.ino, scrappy_junior_suiveur.ino]
